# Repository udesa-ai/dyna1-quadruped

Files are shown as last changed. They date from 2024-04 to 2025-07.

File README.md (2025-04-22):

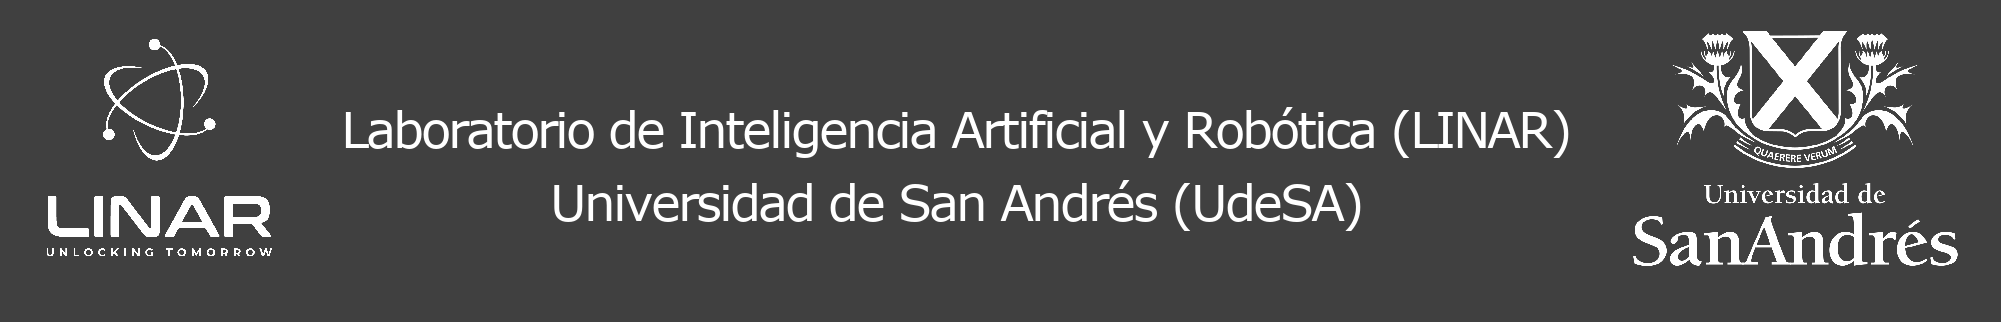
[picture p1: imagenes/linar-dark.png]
Linar

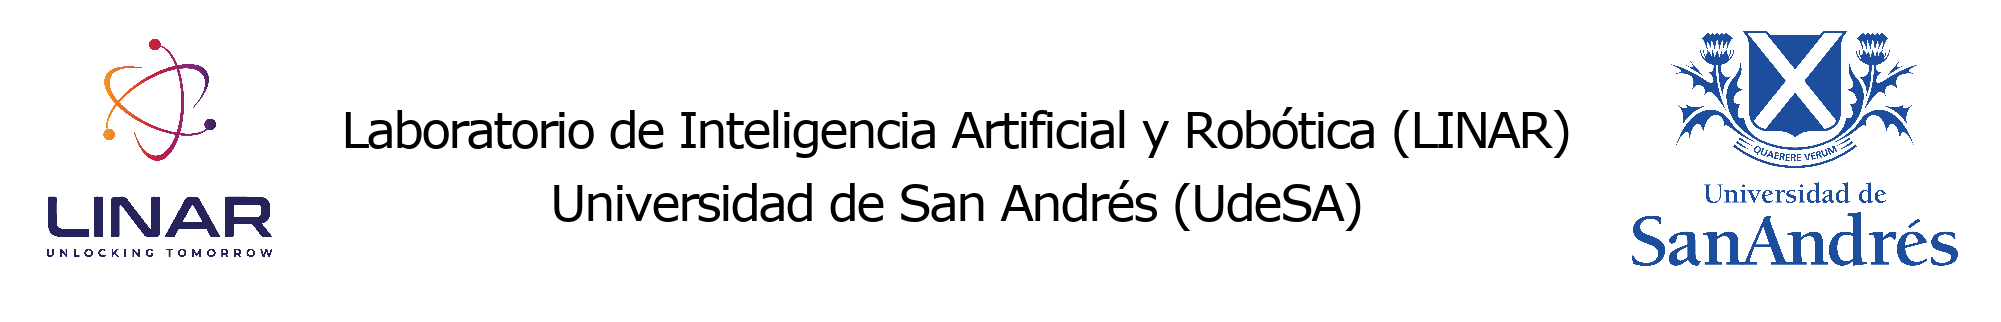
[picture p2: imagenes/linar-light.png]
Linar


<h1 align="center">Dyna1</h3>

<h3 align="center">Plataforma cuadrúpeda para evaluación de algorítmos de locomoción autónom</h3>

<p align="center">
  <a href="https://github.com#gh-light-mode-only">
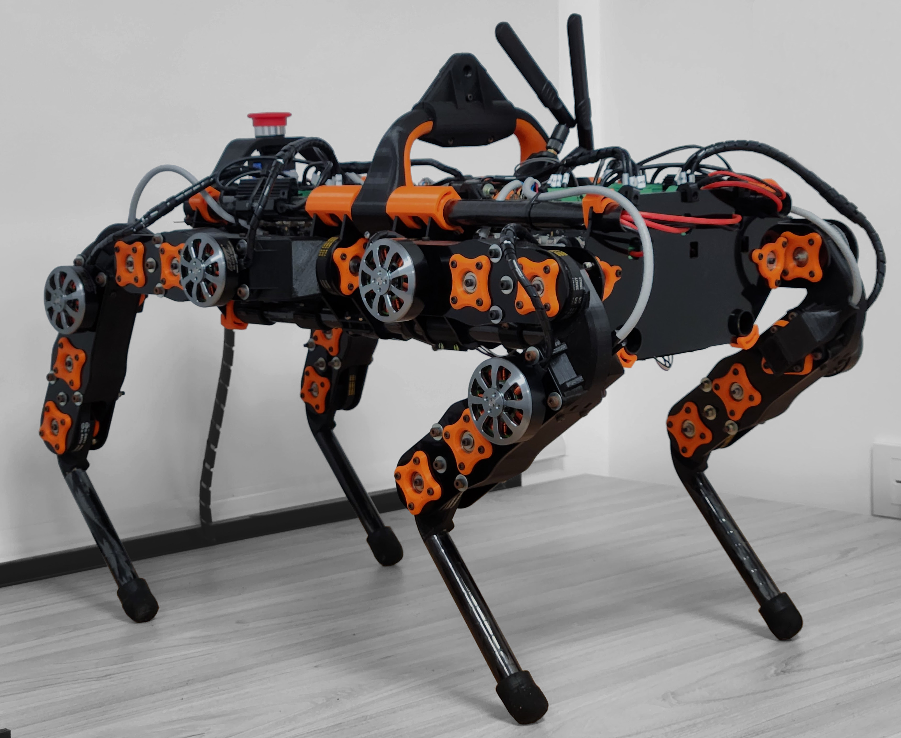
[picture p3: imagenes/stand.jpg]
    
  </a>
  <a href="https://github.com#gh-dark-mode-only">
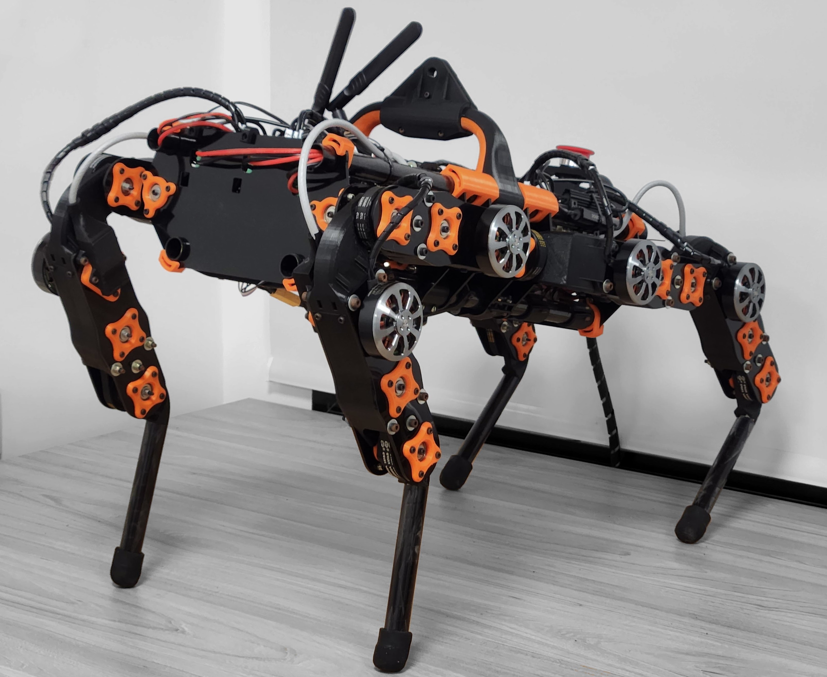
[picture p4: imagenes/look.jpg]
    
  </a>
</p>

## Descripción
<p align="justify"> Presentamos un nuevo diseño de cuadrúpedo de 12 grados de libertad, centrado en reducir el costo y la complejidad de fabricación, y maximizar el uso de componentes disponibles regionalmente. Para facilitar el ensamblado las piernas son modulares, y los motores están lo mas cerca posible del cuerpo para reducir su inercia. Se utilizan motores brushless junto a los controladores Odrive que permiten un control simple con su interfaz por CAN. El cuerpo contiene los motores de los hombros y toda la electónica necesaria para su funcionamiento. La estructura del mismo consta de cuatro barras y placas de acrílico transversales. Para controlar el cuadrúpedo se implementa el sistema operativo ROS2. Todos los proceso cruciales para el funcionamiento del robot se corren en la computadora a bordo, y los demas en la computadora externa. Se demostró experimentalmente que la pierna es capaz de saltar hasta 30 cm con un peso similar a un cuarto del cuerpo. La el período de control (12 ms) y medición (10 ms) se alcanza con un desvío estándar de 0.135 ms y 0.246 ms respectivamente, y las corriente RMS al caminar ronda los 15 A en el motor más exigido, por lo que no debería tener problemas de calentamiento. Se creó un simulador en Pybullet para evaluar algoritmos de autonomía de manera eficiente.  </p>

## Hardware

Los modelos 3d del robot pueden encontrarse en el siguiente link de drive: [LINK](https://drive.google.com/drive/folders/1FCLbqZc1CY9Qmqhhmpl-5FUQIIOlaMu-?usp=sharing).

En la carpeta se pueden encontrar los modelos en formato:
- Fusion 360 (.f3d)
- Step (.stp)

También podrán encontrar el listado de componentes en la carpeta de Hardware de este repositorio, como a su vez el instructivo de construcción y armado del robót.

## Software

La carpeta de Software contiene todas las clases de Python necesarias para el proceso de calibración e iniciación del cuadrúpedo, los paquetes de ROS2, y las instrucciones de uso.

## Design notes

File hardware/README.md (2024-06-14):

### Intervención de motores

Los motores brushless ML5010 y la mayoría de los motores brushless tienen el eje muy corto. 

<p align="center">
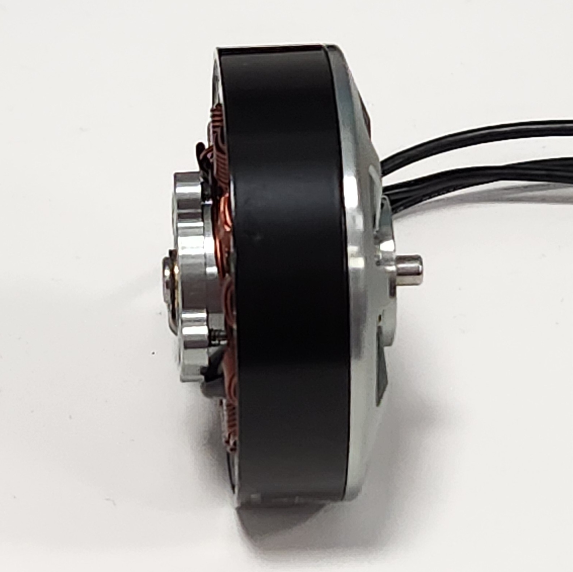
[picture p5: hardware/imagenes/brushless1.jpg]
  
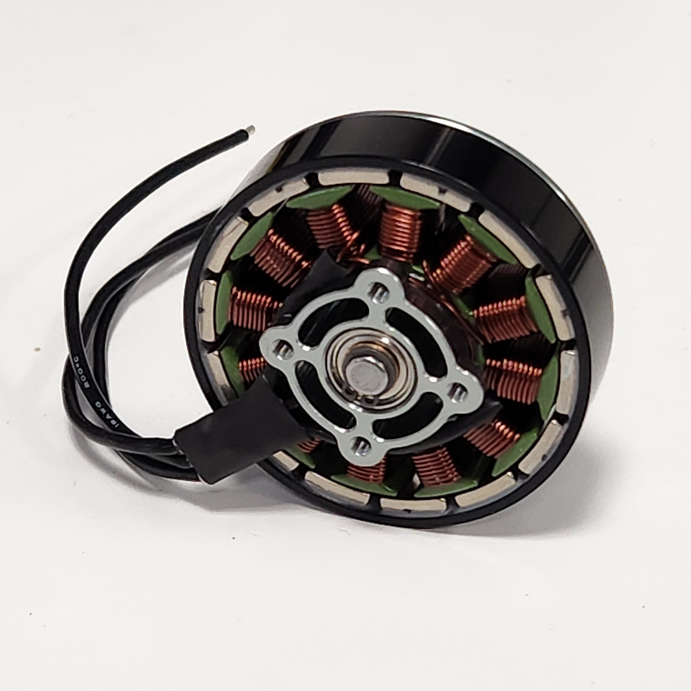
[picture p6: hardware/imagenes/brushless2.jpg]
  
</p>

Es por esto que es necesario removerlo y reemplazarlo por otro. En el caso de los ML5010 primero hay que remover la arandela que sostiene el cuerpo del motor. El eje se sostiene a la corona de imanes por medio de fricción y un prisionero. Un esquema del como debe ser el eje que lo reemplace puede encontrarse en esta carpeta. Se recomienda que le agregue conectores bullet a los cables de las tres faces para su posterior conección con los controladores.

### Metodología de armado general

Con el motoro intervenido podemos comenzar a armar el módulo reductor. A seguir se presenta la metodología estándar. Para formar todos los módulos o el cuerpo se podrá seguir estos pasos, modificando que piezas de utilizan. 

#### Paso 1

Primero se agregan las tuercas M3 a la pieza trasera del módulo, como a su vez los bulones que sostendrán al motor brushless. Se recomienda asegurar que los bulones pueden rotar libremente sin fuerza para facilitar la posterior instalación del motor.

<p align="center">
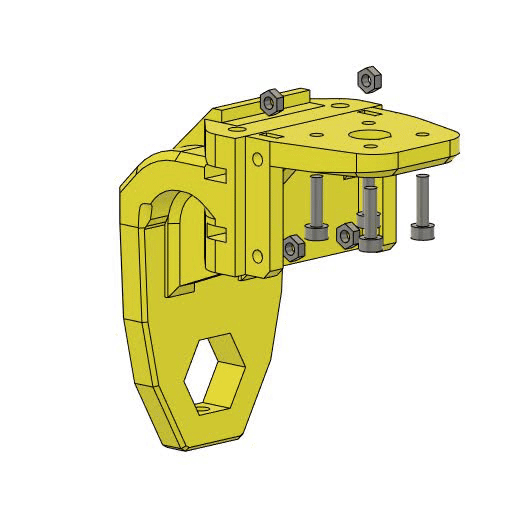
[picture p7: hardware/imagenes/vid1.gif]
  
</p>

#### Paso 2

A seguir se puede colocar la placa superior, los bulones que la sostienen y el motor brushless. Es importante colocar los bulones de la placa primero ya que con el motor instalado no se pueden agregar.

<p align="center">
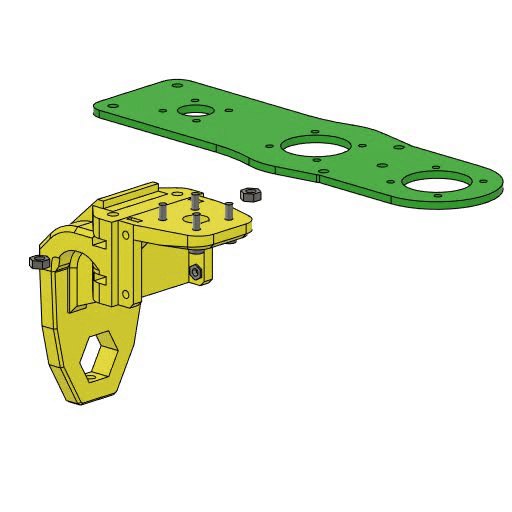
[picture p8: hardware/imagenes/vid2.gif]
  
</p>

#### Paso 3

Antes de colocar la primera polea se recomienda colocar las tuercas M2.5 y los bulones M2.5. Asegurese de que no se restrinja el paso del eje del motor dejando los bulones unos mm fuera de su rosca máxima.

<p align="center">
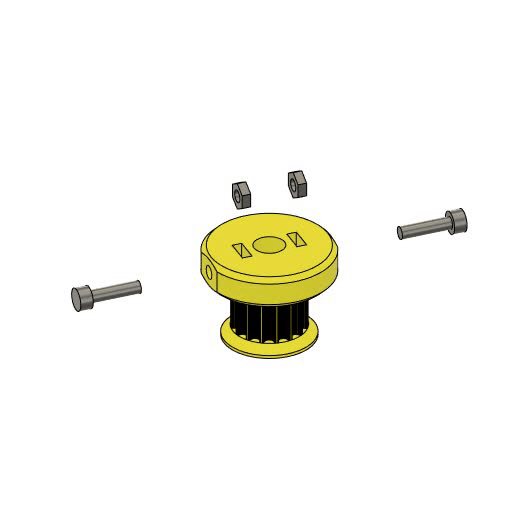
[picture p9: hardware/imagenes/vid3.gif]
  
</p>

#### Paso 4

Coloque las tuercas M2.5 en el alojamiento del encoder. Luego encastre el rodamiento 626zz. Inserte la polea inicial al eje del motor, agregue la correa y coloque la placa inferior. A seguir coloque el alojamiento y asegurelo con los bulones y tuercas M3.

<p align="center">
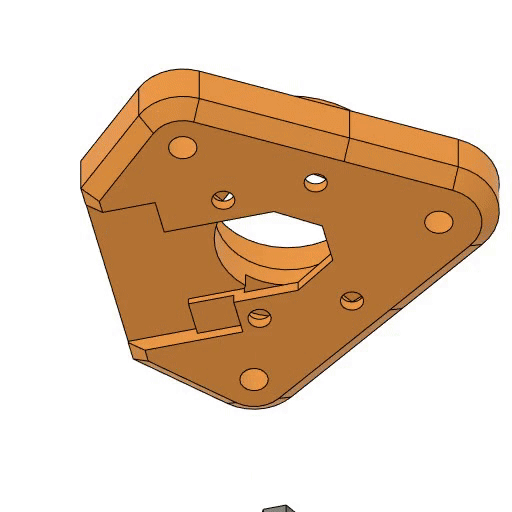
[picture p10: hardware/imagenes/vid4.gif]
  
</p>

#### Paso 5

Para facilitar la instalación del imán puede imprimir la pieza cilíndrica. Se recomienda además agregar una gota de loctite al momento de instalar para que el iman quede fijo al eje. Asegurese de que el pegamento no pase al rodamiento y que además el imán quede correctamente centrado para no perjudicar la medición del encoder.

<p align="center">
  
</p>

Ahora que ya colocó el imán se recomienda calibrar el Odrive y el motor corriendo las instrucciónes [oficiales](https://docs.odriverobotics.com/v/0.5.4/getting-started.html). No se olvide de configurar el index de CAN de los ejes del Odrive para poder comunicarse posteriormente por el bus CAN. El número de index de cada motor puede encontrarlo en el archivo "config.json".

#### Paso 6

Se recomienda colocar la polea central ya armada. Para eso agreuge los rodamientos a cada lado y comprima con el bulon M3. Luego inserte el rodamiento dentro del módulo. Asegurese de colocar correctamente la primera y segunda correa. Sostenga a la polea con los alojamientos. Para tensionar la correa puede rotar los alojamientos en las orientaciones marcadas. Cuanto mayor el número que apunta al motor más tensionada estará la correa. Para nuestro robot la primer polea se encuentra en posición 1 y la segunda en posición 2.

<p align="center">
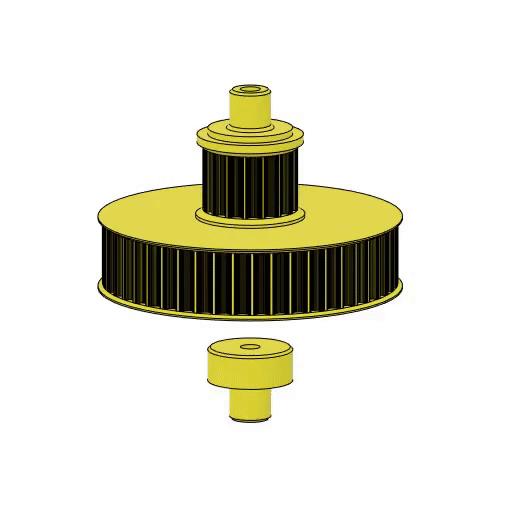
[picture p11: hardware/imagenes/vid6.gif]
  
</p>

#### Paso 7

Coloque la pieza central del módulo y la última polea. Asegurese de que quede bien encastrada la correa. Agregue los alojamientos y fíjelos. Agregue los bulones M4 y las placas laterales para rigidizar la estructura. No olvide atornillar los extremos traseros de las placas laterales.

<p align="center">
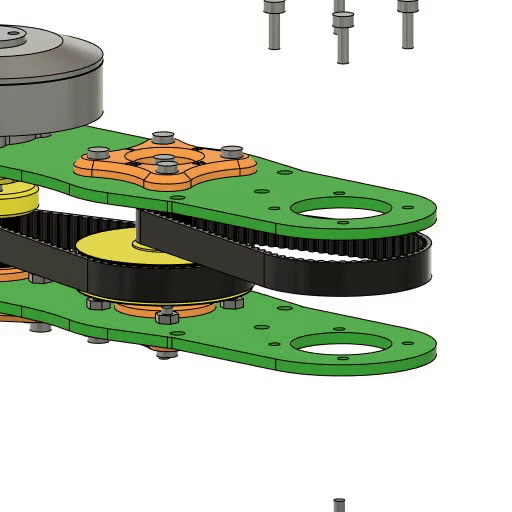
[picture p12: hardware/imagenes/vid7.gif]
  
</p>

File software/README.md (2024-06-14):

### Proceso de Iniciación

A seguir se presenta el paso a paso para inicializar el cuadrúpedo.

#### Paso 1

Corra el código de bash de "can_setup.sh" para activar el puerto CAN de la TX2:

```
./can_setup.sh
```

#### Paso 2

Reinicie los odrive con los motores en las posiciones que utilizará de referencia para cada inicialización.

```
python3 reboot.py
```

#### Paso 3

Una vez reiniciadas y orientadas las piernas corra el código "firmware_workaround.py" para activar el sensado de ángulo. 

```
python3 firmware_workaround.py
```

#### Paso 4

Si nunca calibró las posiciones de los encoder con la de las piernas corra el código de python "calibrate.py". A medida que le pregunte si está listo para calibrar cada pierna, posiciones las en el punto de referencia que decida utilizar.

```
python3 calibrate.py
```

#### Paso 5

Ahora con el robot calibrado y puesto en punto puede abrir el docker de Ubuntu 22 del Dockerfile y ahi correr ROS2 con los launch files.

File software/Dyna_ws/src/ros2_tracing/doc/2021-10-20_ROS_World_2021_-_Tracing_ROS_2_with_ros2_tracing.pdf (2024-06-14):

# Tracing ROS 2 with ros2_tracing

# Christophe Bédard

## ROS World 2021 October 20, 2021

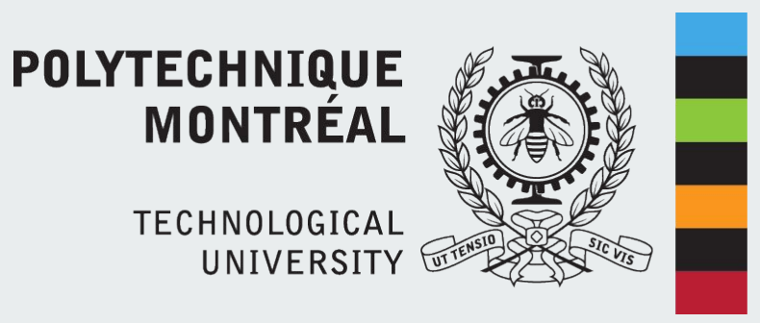
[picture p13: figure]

## DORSAL Laboratory Polytechnique Montréal

Tracing ROS 2 with ros2_tracing - Christophe Bédard

# Plan

### 1. Introduction 2. Context 3. Tracing & LTTng

4. ros2_tracing

### 5. Analysis 6. Demo 7. Conclusion 8. Questions

# Introduction

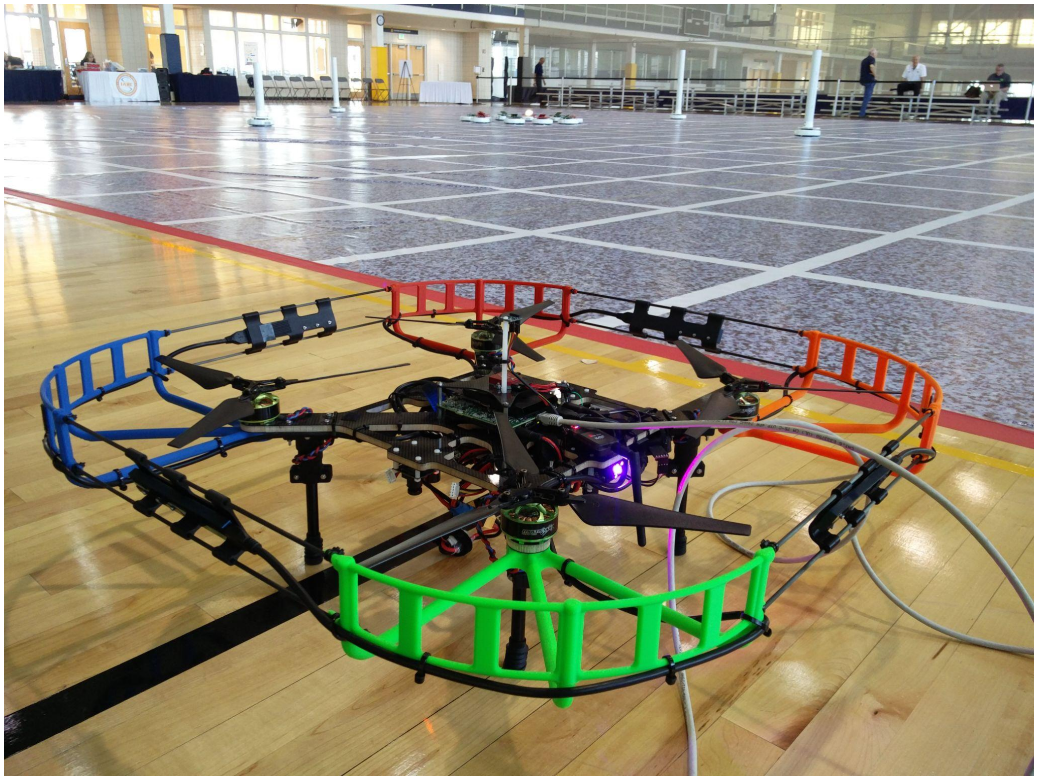
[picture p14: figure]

### - Robotics

- Many different types of applications
- Toys, commercial applications, industrial applications
- Safety-critical systems

### - ROS 2

- New capabilities
- Distributed systems
- Real-time constraints

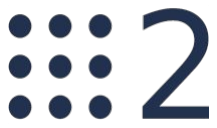
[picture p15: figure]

Context ● | Debugging and diagnostics tools ○ | Debugging: GDB ○ | Logs: ROS, printf() ○ | Introspection: rqt_graph ○ | Others: diagnostic_aggregator, libstatistics_collector ● | Distributed systems ○ | How to analyze a distributed system? ● | Real-time, production ● | Observability problems ○ | Observer effect ○ | Have to avoid influencing or affecting the application ● | Observing an application’s (lack of) determinism ○ | See Ingo Lütkebohle's ROSCon 2017 talk about determinism in ROS:

doi.org/10.36288/ROSCon2017-900789
- See also his talk at the ROSCon 2019 real-time workshop: apex.ai/roscon2019

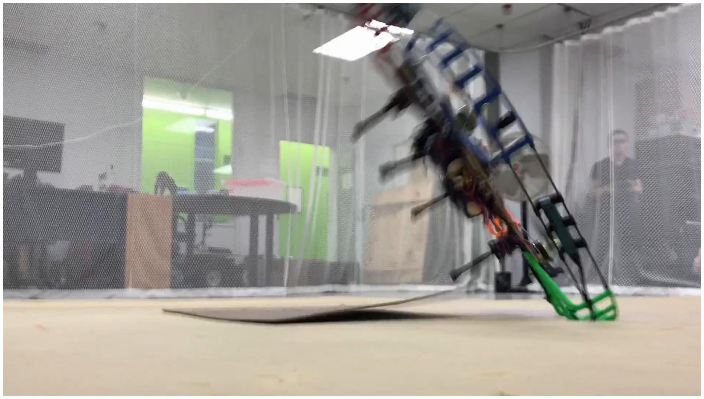
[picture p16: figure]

# Tracing

### - Goal: gather runtime execution information

- Low-level information
- OS and application

### - Useful when issues are hard to reproduce - Many different tracers with different features

- LTTng, perf, Ftrace, eBPF, DTrace, SystemTap, Event Tracing for Windows, etc.

### - Workflow (static instrumentation)

- Instrument an application with trace points
- Configure tracer, run the application
- Trace points generate events (information)
- Events make up a trace

### - We want to minimize the overhead!

- To use in production
- Observer effect

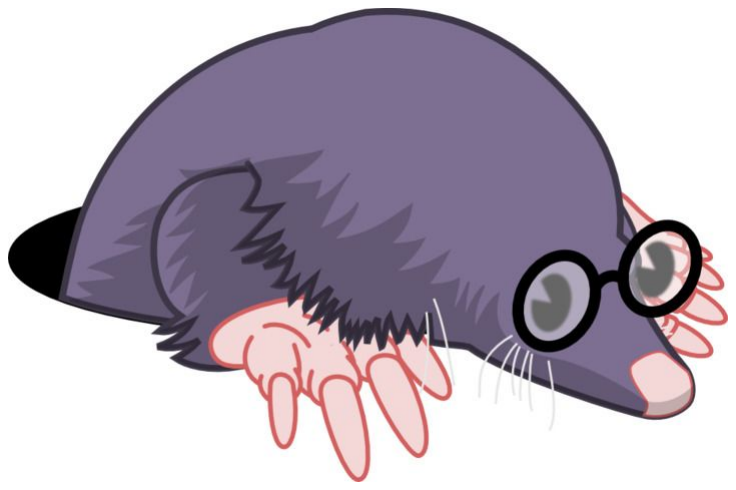
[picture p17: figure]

# LTTng

### - lttng.org - High-performance tracer

- Low overhead
- Userspace tracer + kernel tracer

### - Linux only - Instrumentation

- Built into the Linux kernel (e.g., sched_switch, net_dev_queue)
- Added statically to your application
- Or by LD_PRELOADing libraries

### - Trace data processing

- Online (live)
- Offline (more common & simpler)

# LTTng - example

$ lttng create ros2-session

$ lttng enable-event --kernel sched_switch

$ lttng enable-event --userspace ros2:rclcpp_publish

$ lttng enable-event --userspace ros2:*

$ lttng start

$ ros2 run package executable

$ lttng stop && lttng destroy

- Creating a tracing session, enabling trace events, tracing our application, and stopping

# LTTng - example (2)

$ babeltrace ros2-session/

sched_switch: { cpu_id = 1 }, { prev_comm = "swapper/1", prev_tid = 0, prev_prio = 20, prev_state = (

"TASK_RUNNING" : container = 0 ), next_comm = "test_ping", next_tid = 416160, next_prio = 20 }

ros2:callback_start: { cpu_id = 1 }, { callback = 0x541190, is_intra_process = 0 }

ros2:rclcpp_publish: { cpu_id = 1 }, { message = 0x5464F0 }

ros2:rcl_publish: { cpu_id = 1 }, { publisher_handle = 0x541A40, message = 0x5464F0 }

ros2:rmw_publish: { cpu_id = 1 }, { message = 0x5464F0 }

ros2:callback_end: { cpu_id = 1 }, { callback = 0x541190 }

### - Viewing the trace: each trace event has a name, timestamp, payload

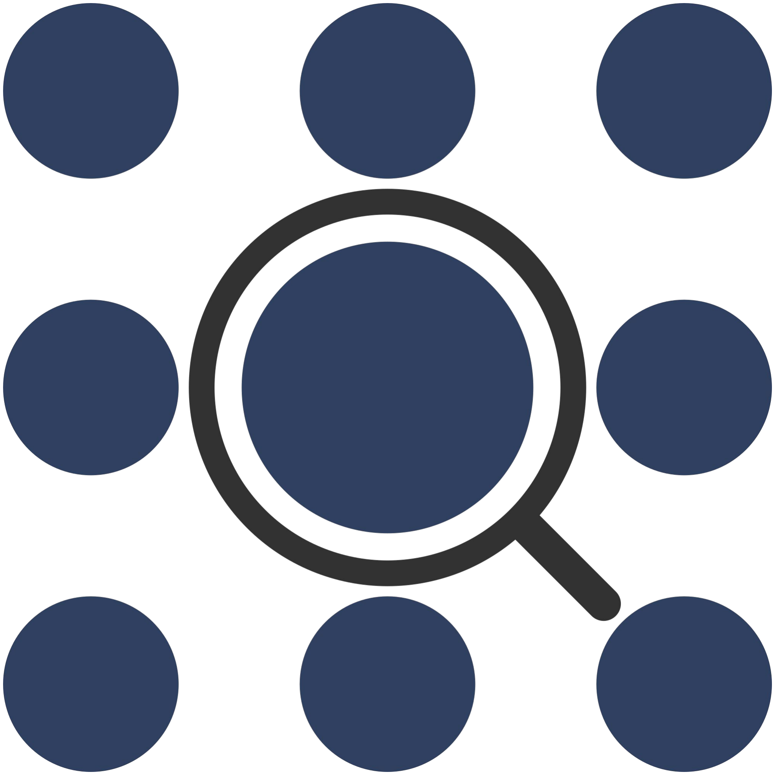
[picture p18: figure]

# ros2_tracing

### - gitlab.com/ros-tracing/ros2_tracing - Collection of tools - Closely integrated into ROS 2

- To promote use and adoption
- Since ROS 2 Eloquent (2019)
- Many improvements and additions since then

### - Tools to instrument the core of ROS 2 with LTTng

- rclcpp, rcl, rmw (rmw_cyclonedds* )

### - Tools to configure tracing with LTTng

- Command: ros2 trace
- Action for ROS 2 launch: Trace

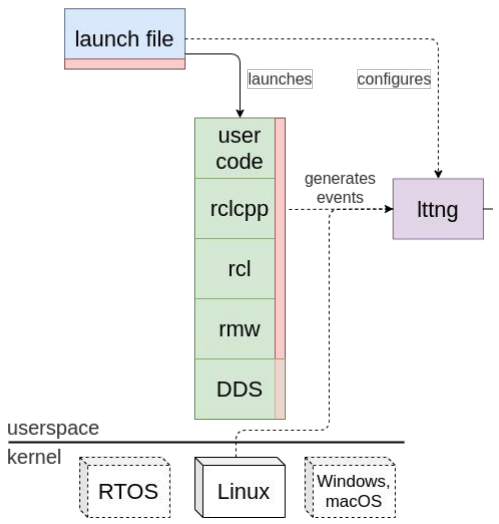
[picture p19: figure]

Figure 1. Instrumentation and general workflow.

# Tools - ros2 trace command

$ ros2 trace \

--session-name ros2-session \

--kernel sched_switch \

--ust ros2:rclcpp_publish ros2:*

writing tracing session to: /home/chris/.ros/tracing/ros2-session

press enter to start...

press enter to stop...

stopping & destroying tracing session

### - To easily start tracing - Starting & stopping is done manually

# Tools - Trace action for ROS 2 launch

from | launch | import | LaunchDescription
from | launch_ros.actions | import | Node
from | tracetools_launch.action | import | Trace
def | generate_launch_description():
return | LaunchDescription([

Trace(

session_name='ros2-session',

events_kernel=['sched_switch'],

events_ust=['ros2:rclcpp_publish', 'ros2:*'],

),

Node(

package='pkg',

executable='exe',

),

])

### - Starts tracing when launched - Stops tracing when exiting - Great for complex systems with multiple nodes

# Tools - Trace action for ROS 2 launch (2)

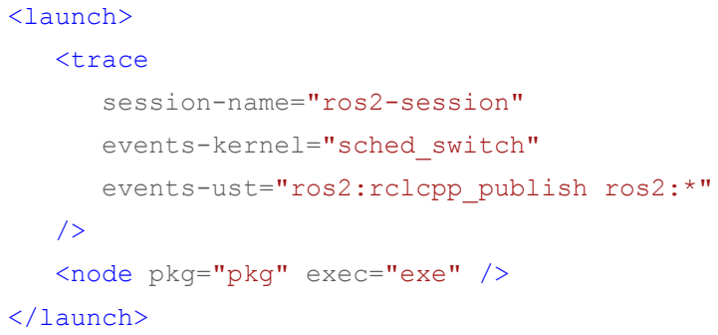
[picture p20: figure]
<launch>; <trace; session-name="ros2-session"; events-kernel="sched_switch"; events-ust="ros2:rclcpp_publish ros2:*"; <node; pkg="pkg"; exec="exe"; </launch>

launch:

- trace:
session-name: | ros2-session
events-kernel: | sched_switch
events-ust: | ros2:rclcpp_publish ros2:*
- node:
pkg: | pkg
exec: | exe

### - Also available in XML and YAML launch files

# Instrumentation

### - Only on Linux, not included in the binaries

- At least for now
- Install LTTng and (re)build the tracetools package

### - Instrumentation was designed to support multiple tracers

- Other tracers and/or OSes, eventually
- rclcpp, rcl, rmw, etc. → tracetools → LTTng

### - Design principles

- Want information about each layer & the interaction between them
- However, layers make it hard to get the full picture
- Need to gather small bits of information here and there
- Put it all together offline or externally

### - Real-time

- Applications generally have a non-real-time initialization phase
- We take advantage of this to collect as much information up front
- It lowers overhead in the real-time “steady state” phase

# Instrumentation (2)

- | Object instances ○ | Node, publisher, subscription, timer ● | Events ○ | Callback execution (subscription, timer) ○ | Message publication ○ | Message taking (for subscription callbacks) ○ | Lifecycle node state change ○ | Internal executor phases ○ | Etc. ● | Applies to most layers ○ | rclcpp, rcl, rmw ○ | DDS (work in progress with Eclipse Cyclone DDS)

ros2:rcl_node_init: { node_handle = | 0x🚀, rmw_handle = 0x..., node_name = "test_ping" }
ros2:rcl_publisher_init: { publisher_handle = | 0x, node_handle = 0x🚀, topic_name = "/ping", queue_depth = 10}
ros2:rcl_timer_init: { timer_handle = | 0x⏲, period = 500000000 }
ros2:rclcpp_timer_callback_added: { timer_handle = | 0x⏲, callback = 0x🤖 }
ros2:rclcpp_callback_register: { callback = | 0x🤖, symbol = "std::_Bind<void (PingNode::*(PingNode*))()>" }
ros2:rclcpp_timer_link_node: { timer_handle = | 0x⏲, node_handle = 0x🚀 }
ros2:callback_start: { callback = | 0x🤖, is_intra_process = 0 }
ros2:rclcpp_publish: { message = | 0x }
ros2:rcl_publish: { message = | 0x, publisher_handle = 0x }
ros2:rmw_publish: { message = | 0x }
ros2:callback_end: { callback = | 0x🤖 }

### - Ping node: a timer is used to publish a message periodically

# Instrumentation - example

# Overhead benchmark

- | Goal: measure tracing overhead in a ROS 2 context ○ | Mainly interested in a latency overhead ○ | Tool: gitlab.com/ApexAI/performance_test ● | Parameters ○ | Inter-process: 1 pub → 1 sub ○ | Publishing: 100 - 2000 Hz ○ | Messages: 1 - 256 KB ○ | Quality of service: reliable ○ | Eclipse Cyclone DDS ● | Setup ○ | Ubuntu Server 20.04.2 with PREEMPT_RT (5.4.3-rt1) ○ | Intel i7-3770 @ 3.40 GHz, 8 GB RAM ○ | SMT/Hyper-threading disabled (4 cores, 1 thread/core) ○ | SCHED_FIFO, RT priority 99, and other tuning ○ | Run for 20 minutes, discard the first 5 seconds

# Overhead benchmark - results

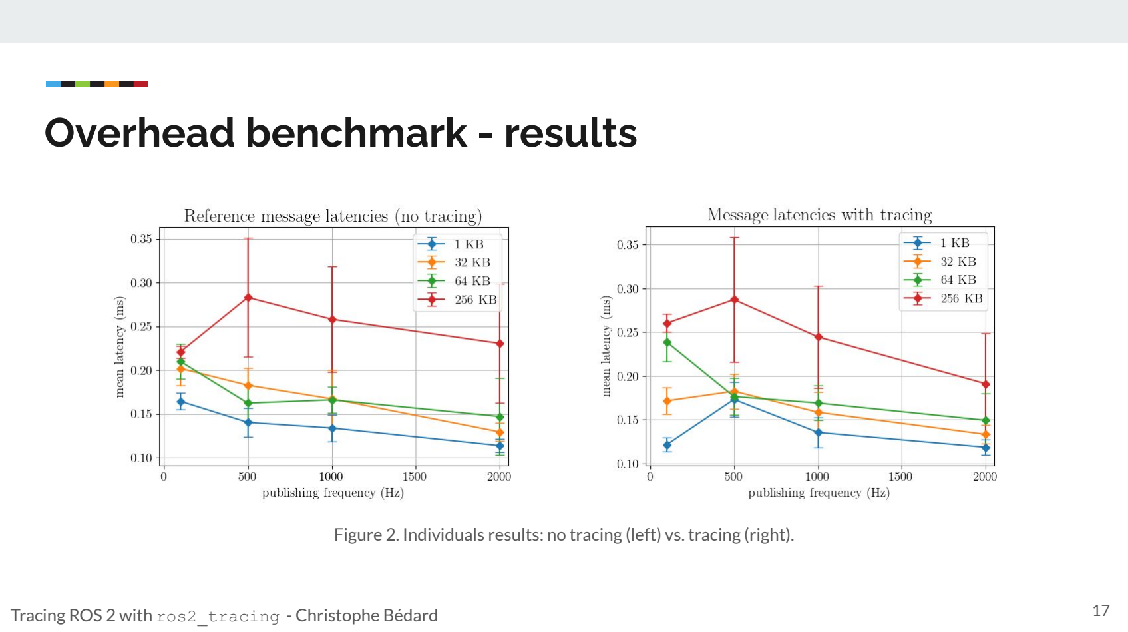
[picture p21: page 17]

Figure 2. Individuals results: no tracing (left) vs. tracing (right).

# Overhead benchmark - results (2)

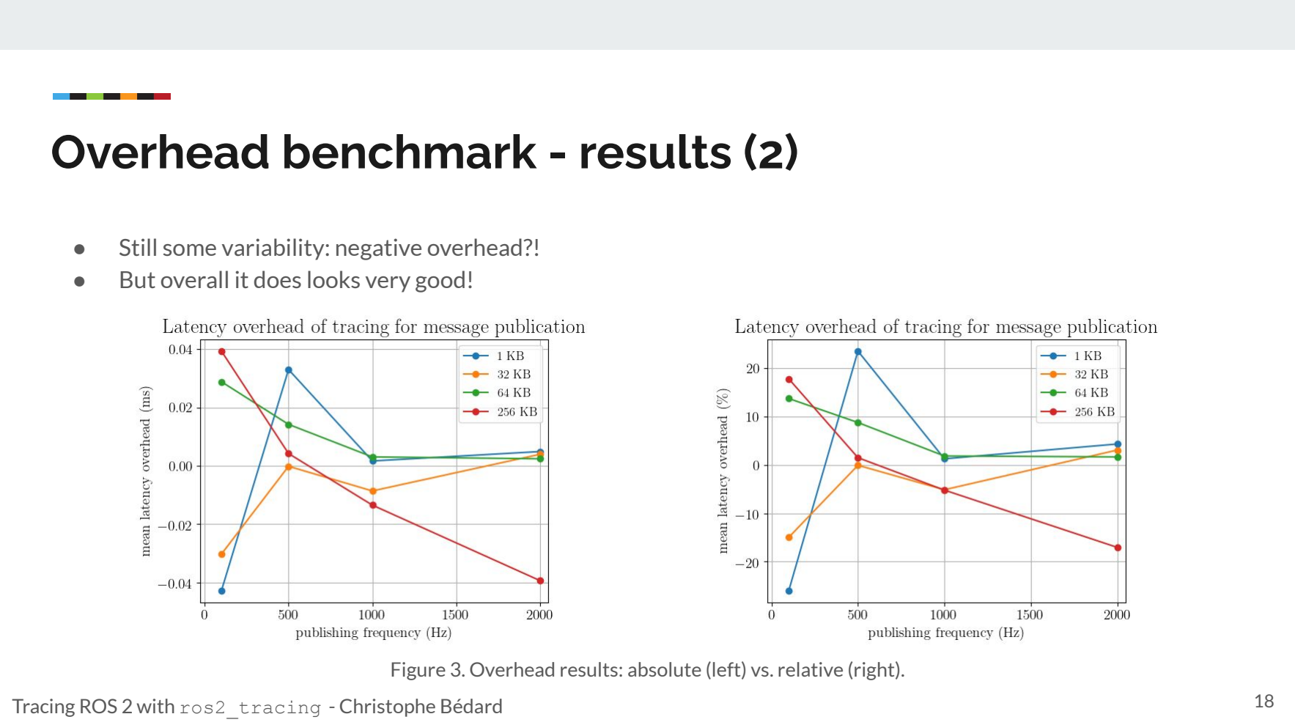
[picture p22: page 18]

### - Still some variability: negative overhead?! - But overall it does looks very good!

Figure 3. Overhead results: absolute (left) vs. relative (right).

# Analysis

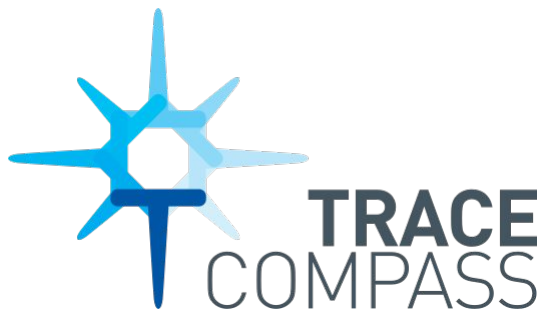
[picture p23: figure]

### - Many tools to analyze traces generated by LTTng

- babeltrace: babeltrace.org
- Trace Compass: tracecompass.org
- tracetools_analysis
- gitlab.com/ros-tracing/tracetools_analysis
- Goal: quick trace analysis
- Simple Python tool
- Pre-processes raw trace data, provides multiple 2D tables as pandas DataFrames
- Offers simple functions to analyze those DataFrames
- Use inside a Jupyter Notebook, or in a simple Python file

### - Advanced analyses

- Correlate ROS 2 trace events with events from the Linux kernel or other applications
- Analyze the aggregation of traces from multiple systems

# Analysis - example

import | tracetools_analysis; | import | bokeh
events = load_file('~/.ros/tracing/pingpong') | # Read the trace
handler = Ros2Handler.process(events) | # (Pre-)process the data

data_util = Ros2DataModelUtil(handler.data)

callback_symbols = data_util.get_callback_symbols() | # Extract callback functions

duration = bokeh.plotting.figure(...)

for | callback, symbol | in | callback_symbols.items(): | # For each callback...

owner_info = data_util.get_callback_owner_info(callback)

if | not | owner_info | or | '/parameter_events' | in | owner_info: | # | Filter out internal subscriptions

continue

duration_df = data_util.get_callback_durations(callback) | # | Get duration data for this callback
duration.line(x='timestamp', y='duration', legend=str(symbol), | # | Add to plot

source=bokeh.models.ColumnDataSource(duration_df))

bokeh.io.show(duration) | # Display final plot

### - Plot callback durations

# Analysis - example (2)

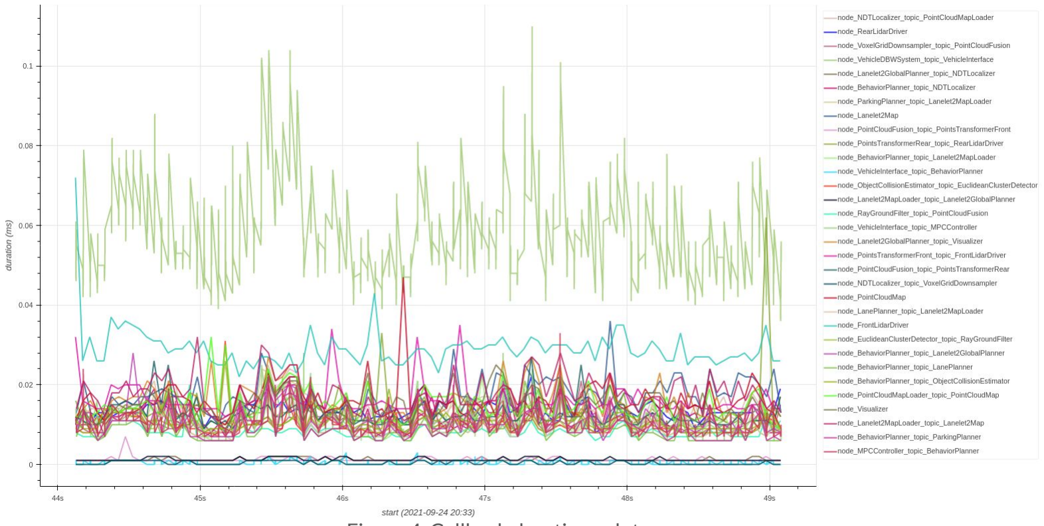
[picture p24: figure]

Figure 4. Callback durations plot.

# Analysis - example (3)

### - Using Trace Compass - Critical path analysis of a wget request - Computes dependencies between threads - Only using data from the Linux kernel

- Blocking system calls

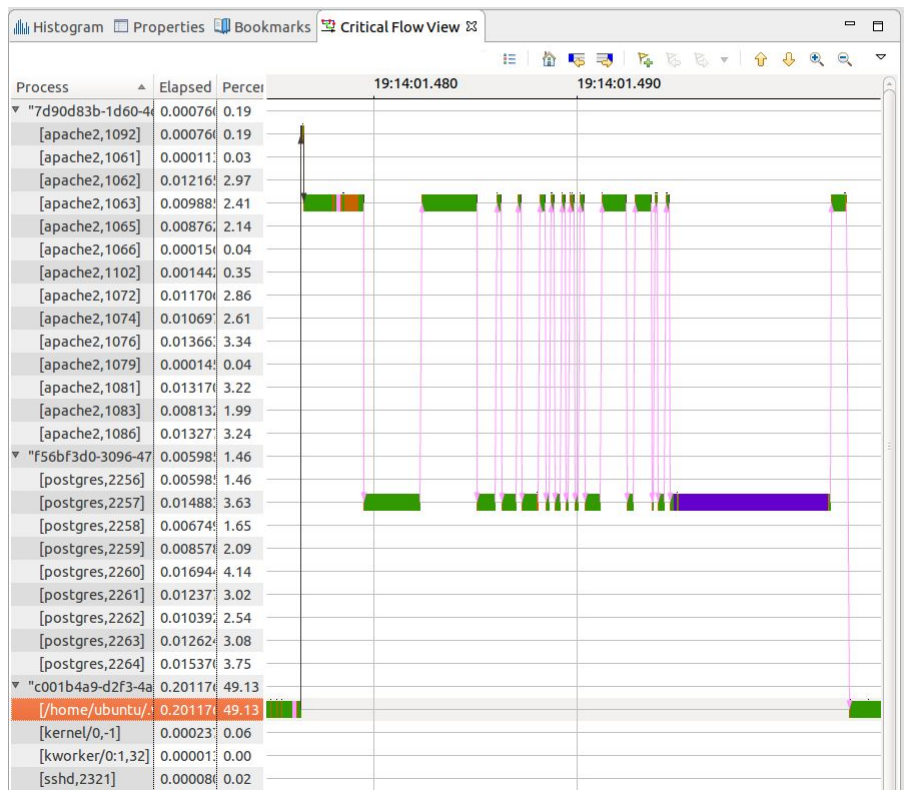
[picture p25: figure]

Figure 5. Critical path analysis using Trace Compass.

# Demo

### - Ping & pong nodes

- Nodes exchange N messages every M milliseconds T times, then exit

### - Link to instructions and Python code in a Jupyter Notebook

- github.com/christophebedard/ros-world-2021-demo

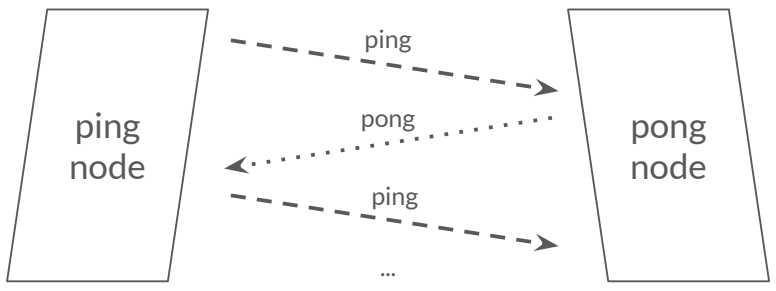
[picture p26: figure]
ping node; pong node; ping; pong

# Demo - results

### - Simple demo, ROS 2-level information only

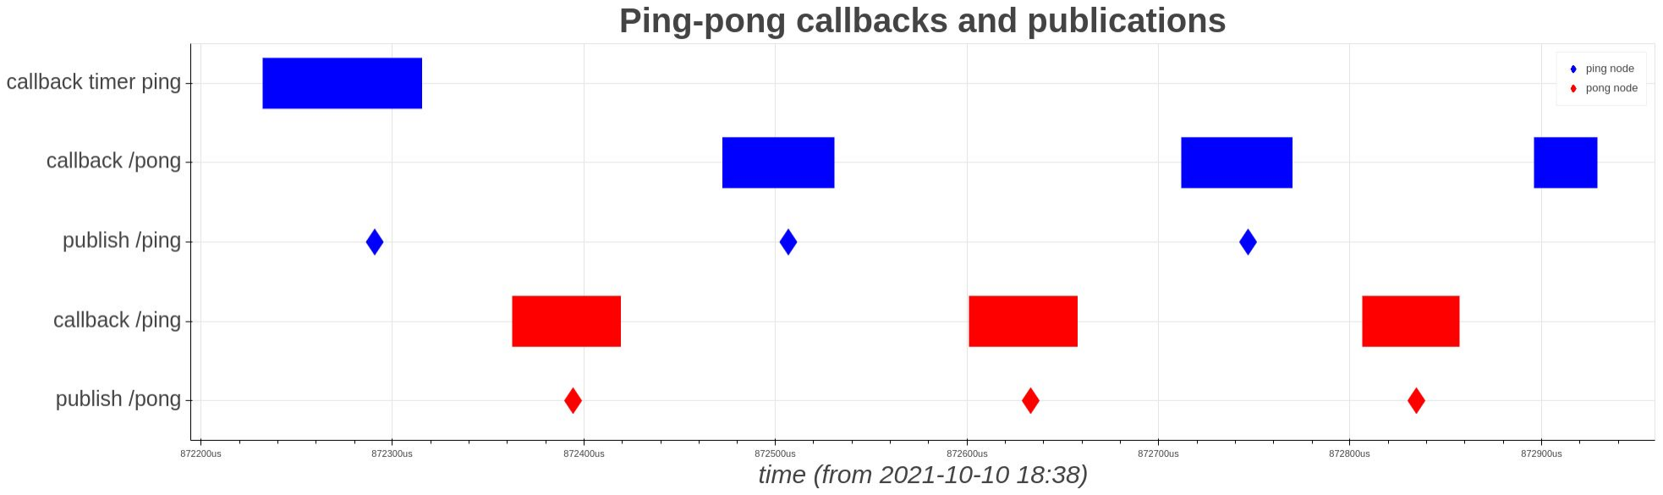
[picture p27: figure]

Figure 6. Results for 1 sequence.

# Demo - results (2)

- Still a lot of information & many possibilities, especially if we add DDS/middleware instrumentation!

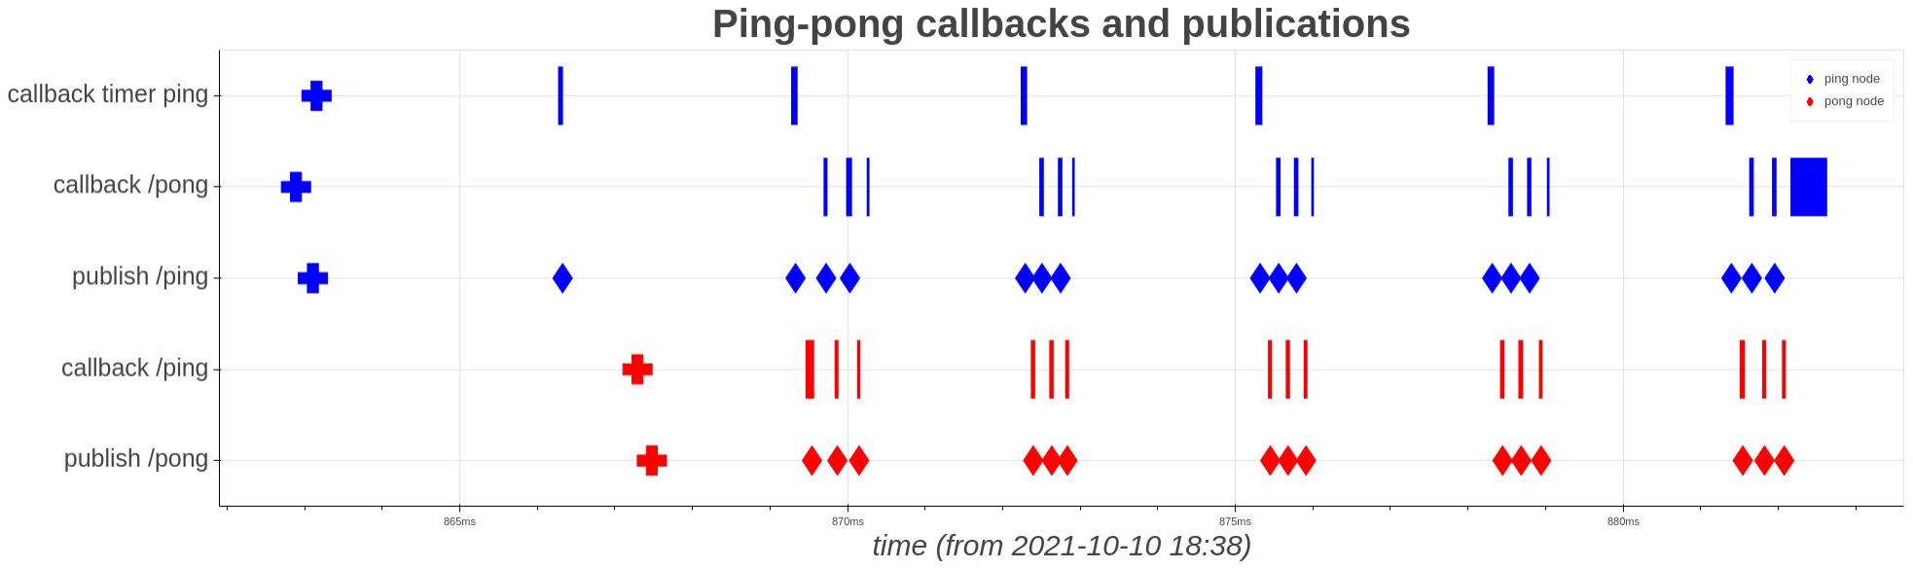
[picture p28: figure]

Figure 7. Overall demo results.

# Conclusion

### - Tracing

- Gather low-level runtime execution information
- Use a low overhead tracer
- ros2_tracing
- Instrumentation for the core of ROS 2
- Tools to trace with LTTng

### - Analysis

- Correlate OS events with ROS 2 events
- Analyze the aggregation of traces from multiple systems

### - Future

- Including the LTTng tracepoints in the Linux binaries
- Instrumentation
■ | Internal handling of messages, tracking messages across nodes
■ | DDS
- What would you like to see?!

Questions?; ● github.com/christophebedard; ● Important links; ○ gitlab.com/ros-tracing/ros2_tracing; ○ lttng.org ○ ros2_tracing tutorial in RTWG docs: bit.ly/RTWG_tracing_tutorial

- gitlab.com/ros-tracing/tracetools_analysis

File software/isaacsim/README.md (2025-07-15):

## Configuración del entorno para Dyna1 en Isaac Sim

### Isaac Lab
**Isaac Lab** es una librería construida sobre Isaac Sim que facilita el desarrollo de entornos de simulación para 
aprendizaje por refuerzo (RL), control óptimo y robótica en general. Se basa en gymnasium, y ofrece herramientas ya integradas para:

- Definir entornos personalizados tipo Gym.
- Entrenar políticas con algoritmos populares como PPO.
- Simular robots con interfaces limpias y separadas.
- Integrarse con librerías de RL como RL-Games, Stable-Baselines3, etc.

#### ¿Por qué usarlo?
- Estandariza cómo definís los entornos, sensores, recompensas y acciones.
- Aísla tu entorno personalizado del resto de Isaac Sim → más fácil de mantener y migrar.
- Ya tiene soporte para entrenamiento distribuido y acelerado por GPU.
- Facilita la transferencia del modelo a un robot real (sim2real).

### Isaac Extension Template
Es una plantilla modular creada para estructurar proyectos en Isaac Sim de forma escalable y mantenible:

Incluye:
- Separación clara entre código, assets, configuraciones.
- Soporte para definir extensiones de OmniIsaacGymEnvs, robots, tareas, sensores, etc.
- Integración con Isaac Lab out-of-the-box.

#### ¿Por qué usarlo?
- Permite trabajar en equipo con una arquitectura limpia y modular.
- Podés agregar o quitar componentes sin romper todo el proyecto.
- Si necesitás escalar, migrar o versionar tu entorno, esto evita el caos.

1. Clonar los repositorios necesarios
    
	    cd ~
	    https://github.com/isaac-sim/IsaacLabExtensionTemplate.git
	    https://github.com/isaac-sim/IsaacLab.git

2. Mover el entorno del Dyna1

    	mv dyna1-quadruped/software/isaacsim/DynabotIsaacTemplate IsaacLabExtensionTemplate/source

**DynabotIsaacTemplate** contiene toda la configuración específica del robot Dyna1 aislada de Isaac Lab. Esto significa que cualquier cambio en Isaac Lab no debería afectar nuestro entorno (en principio), manteniendo todo modular y desacoplado.

3. Editar el archivo en **IsaacLab/docker/docker-compose.yaml** y agregar estas líneas dentro de la sección binds del servicio (al final de esa lista):

		- type: bind
		source: /home/$USER/IsaacLabExtensionTemplate
		target: /workspace/IsaacLabExtensionTemplate

¿Qué hace esto?

- **type: bind:** Monta un volumen directamente desde el sistema de archivos del host.
- **source:** Ruta local donde está el proyecto (reemplazá $USER por tu nombre de usuario si no funciona).
- **target:** Ruta dentro del contenedor donde se verá esa carpeta.

4.  Iniciar el contenedor
   
   		./container.sh start

Es posible que la primera vez te aparezca este mensaje (ver Troubleshooting):

    X11 Forwarding is configured as '0' in '.container.cfg'.
	To enable X11 forwarding, set 'X11_FORWARDING_ENABLED=1' in '.container.cfg'.

5. Ingresar al contenedor

		./container.sh enter base

y una vez dentro del docker hacer:

    cd /workspace/IsaacLabExtensionTemplate/

6. Instalar todas las dependencias del Dyna1:

		python -m pip install -e source/DynabotIsaacTemplate

Si falla el paso anterior es poque probablemente antes haya que actualizar pip a la ultima version:

    /workspace/isaaclab/_isaac_sim/kit/python/bin/python3 -m pip install --upgrade pip

7. Si se quire correr la simulación en una máquina y visualizarla desde otra, exportá esta variable:

    	export LIVESTREAM=2

Esto es por si se esta usando una PC para correr el entrenamiento y se quiere visualizar el output de la simulacion desde otra.

8. Modificar import en script de entrenamiento

Editar la línea 68 del archivo IsaacLabExtensionTemplate/scripts/rsl_rl/train.py:

Antes:

	import ext_template.tasks  # noqa: F401

Después:
    
    import DynabotIsaacTemplate.tasks  # noqa: F401

9. Correr la simulación del Dyna1

Si todo fue bien (aunque probablemente algo haya que ajustar), lanzar la simulación con:

    python scripts/rsl_rl/train.py --task=Dyna1-Flat-v0 --headless --num_envs=32

Este comando indica que se va a lanzar la simulacion con terrenos **flat**, de manera **headless** con 32 robots. 

## Troubleshooting

- Si la simulación no se lanza en headless desde docker, puede ser que esté intentando hacer forward del GUI y crashee (porque tenés deshabilitado x11).
- Configurar esto en **isaacLab/docker/.container.cfg**:
  
      [X11]
      x11_forwarding_enabled = 0

- En uno de sus commits los genios de IsaacLab modificaron como hydra parsea atributos y tiro este error:

		usage: train.py [--help] [--hydra-help] [--version] [--cfg {job,hydra,all}] [--resolve] [--package PACKAGE] [--run] [--multirun] [--shell-completion] [--config-path CONFIG_PATH] [--config-name CONFIG_NAME] [--config-dir CONFIG_DIR] [--experimental-rerun EXPERIMENTAL_RERUN] [--info [{all,config,defaults,defaults-tree,plugins,searchpath}]] [overrides ...]
		train.py: error: unrecognized arguments: --/app/livestream/allowResize=false

- Por lo que debuggee esta linea en **train.py**:

		app_launcher = AppLauncher(args_cli)
 
 inyecta el argumento --/app/livestream/allowResize=false dentro de sys.argv. 
 
 - Agregar este filtrado después de la línea en la que se crea AppLauncher resuelve el problema.

		...
		app_launcher = AppLauncher(args_cli)
		simulation_app = app_launcher.app
		
		# Filter out AppLauncher-injected args before Hydra sees them
		sys.argv = [sys.argv[0]] + [arg for arg in hydra_args if not arg.startswith("--/")]
		...

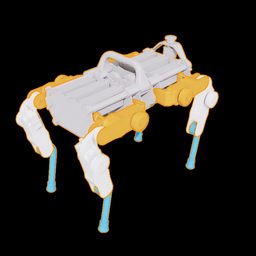
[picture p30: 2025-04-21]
software/isaacsim/DynabotIsaacTemplate/assets/urdf/dyna1/.thumbs/256x256/dyna1.usd.png

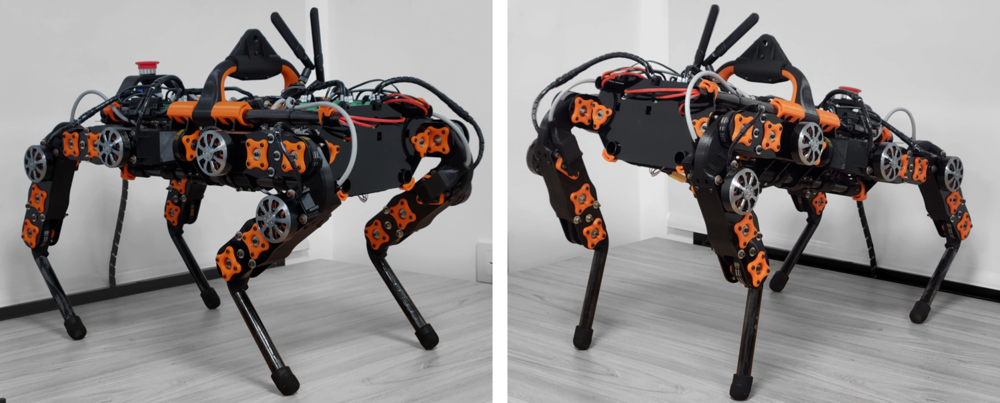
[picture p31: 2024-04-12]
imagenes/dog.png

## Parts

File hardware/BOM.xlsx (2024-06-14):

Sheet: Totales
Sub-Conjunto | Cantidad | Peso | Precio | Peso Total
Link 1 | 4 | 0.519 | $81.41 | 2.075 | Precio Dólar | 996.61
Link 2 | 4 | 0.515 | $80.92 | 2.058 | (al momento de armar la tabla)
Link 3 | 4 | 0.067 | $0.59 | 0.267
Cuerpo | 1 | 3.655 | $2672.97 | 3.655
 |  |  | $2835.89 | 8.055

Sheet: Modulo Link 1
Número | Nombre | Productor | Código Productor | Comentario | Link | Precio US$ | Precio AR$ | Peso [kg] | Cantidad | Total Precio US$ | Total Peso [kg]
1 | Motor | GARTT | ML 5010 300KV | - |  | $34.22 |  | 0.193 | 1 | $34.22 | 0.193
2 | Eje motor | UdeSA | - | 6mm de diámetro |  |  | $498.84 | 0.003 | 1 | $0.50 | 0.003
3 | Placa Superior |  | - | 3mm de espesor |  |  | $757.94 | 0.023 | 1 | $0.76 | 0.023
4 | Placa Inferior |  | - | 3mm de espesor |  |  | $719.14 | 0.022 | 1 | $0.72 | 0.022
5 | Correa | Gates | 3MR-255 | A definir en base a disponibilidad. Peso estimado |  |  | $11247.60 | 0.006 | 2 | $22.57 | 0.012
6 | Eje Central | I3D | - | Se asume densidad del 50% para PLA |  |  | $240.15 | 0.012 | 1 | $0.24 | 0.012
7 | Encoder | AMS | AS5047P | - | Link (https://www.mouser.co.uk/ProductDetail/ams/AS5047P-TS_EK_AB/?qs=Rt6VE0PE%2FOfJKFTMKo%252BL0Q==) | $15.75 |  | 0.017 | 1 | $15.75 | 0.017
8 | Alojamiento Rodamiento 1 | I3D | - | Se asume densidad del 50% para PLA |  |  | $62.31 | 0.003 | 4 | $0.25 | 0.013
9 | Rodamiento | SKF | W 626-2Z | - |  |  | $755.60 | 0.008 | 5 | $3.79 | 0.040
10 | Arandela M3 |  | - | - |  |  |  | 0.0004 | 8 | $0.00 | 0.004
11 | Tuerca M3 |  | 604 000 | - |  |  |  | 0.0004 | 22 | $0.00 | 0.009
12 | Tornillo Allen Boton M3x10 |  | OBAA00310 FOS | - |  |  |  | 0.0008 | 21 | $0.00 | 0.017
13 | Alojamiento Rodamiento 2 | I3D | - | Se asume densidad del 50% para PLA |  |  | $112.86 | 0.006 | 1 | $0.11 | 0.006
14 | Tuerca M2.5 |  | - | - |  |  |  | 0.0003 | 6 | $0.00 | 0.002
15 | Tornillo Allen Boton M2.5x5 |  | - | Revisar |  |  |  | 0.0005 | 4 | $0.00 | 0.002
16 | Engranaje Inicial | I3D | - | Se asume densidad del 50% para PLA |  |  | $53.32 | 0.003 | 1 | $0.05 | 0.003
17 | Tornillo Allen M2.5x12 |  |  | - |  |  |  | 0.0007 | 2 | $0.00 | 0.001
18 | Tapas plásticas | I3D | - | Se asume densidad del 50% para PLA |  |  | $572.83 | 0.0289 | 1 | $0.57 | 0.029
19 | Tornillo Allen Boton M3x16 |  | - | - |  |  |  | 0.0011 | 3 | $0.00 | 0.003
20 | Tornillo Allen Boton M4x16 |  | - | - |  |  |  | 0.002 | 5 | $0.00 | 0.011
21 | Toma Trasera | I3D | - | Se asume densidad del 50% para PLA |  |  | $877.26 | 0.044 | 1 | $0.88 | 0.044
22 | Tornillo Allen Boton M3x12 |  | - | - |  |  |  | 0.001 | 4 | $0.00 | 0.004
23 | Tuerca M4 |  | - | - |  |  |  | 0.001 | 4 | $0.00 | 0.003
24 | Barra de Aluminio 1 |  | - | - |  |  | $268.00 | 0.004 | 2 | $0.54 | 0.007
25 | Barra de Aluminio 2 |  | - | - |  |  | $172.00 | 0.002 | 1 | $0.17 | 0.002
26 | Tornillo Allen Boton M4x50 |  | - | - |  |  |  | 0.003 | 3 | $0.00 | 0.010
27 | Eje Hombro |  |  |  |  |  | $47.54 | 0.002 | 1 | $0.05 | 0.002
28 | Prisionero M3x6 |  | - | - |  |  |  | 0.0003 | 1 | $0.00 | 0.000301
29 | Tornillo Allen Boton M4x20 |  | - | - |  |  |  | 0.002 | 2 | $0.00 | 0.005
30 | Acomple Hombro | I3D | - | Se asume densidad del 50% para PLA |  |  | $224.35 | 0.011 | 1 | $0.23 | 0.011
31 | Arandela M4 |  |  |  |  |  |  | 0.001 | 3 | $0.00 | 0.002
32 | Tornillo Allen M3x50 |  |  |  |  |  |  | 0.003 | 2 | $0.00 | 0.007
 |  |  |  |  |  |  |  |  |  | $0.00 | 0.000
 |  |  |  |  |  |  |  |  |  | $0.00 | 0.000
 |  |  |  |  |  |  |  |  |  | $0.00 | 0.000
 |  |  |  |  |  |  |  |  |  | $0.00 | 0.000
 |  |  |  |  |  |  |  |  |  | $0.00 | 0.000
 |  |  |  |  |  |  |  |  |  | $0.00 | 0.000
 |  |  |  |  |  |  |  |  |  | $81.41 | 0.5187806093

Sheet: Modulo Link 2
Número | Nombre | Productor | Código Productor | Comentario | Link | Precio US$ | Precio AR$ | Peso [kg] | Cantidad | Total Precio US$ | Total Peso [kg]
1 | Motor | GARTT | ML 5010 300KV | - |  | $34.22 |  | 0.193 | 1 | $34.22 | 0.193
2 | Eje motor | UdeSA | - | 6mm de diámetro |  |  | $498.84 | 0.003 | 1 | $0.50 | 0.003
3 | Placa Superior | Mundo Acrilico | - | 3mm de espesor |  |  | $757.94 | 0.023 | 1 | $0.76 | 0.023
4 | Placa Inferior | Mundo Acrilico | - | 3mm de espesor |  |  | $719.14 | 0.022 | 1 | $0.72 | 0.022
5 | Correa | Gates | 3MR-255 | A definir en base a disponibilidad. Peso estimado |  |  | $11247.60 | 0.006 | 2 | $22.57 | 0.012
6 | Eje Central | I3D | - | Se asume densidad del 50% para PLA |  |  | $240.15 | 0.012 | 1 | $0.24 | 0.012
7 | Encoder | AMS | AS5047P | - | Link (https://www.mouser.co.uk/ProductDetail/ams/AS5047P-TS_EK_AB/?qs=Rt6VE0PE%2FOfJKFTMKo%252BL0Q==) | $15.75 |  | 0.017 | 1 | $15.75 | 0.017
8 | Alojamiento Rodamiento 1 | I3D | - | Se asume densidad del 50% para PLA |  |  | $62.31 | 0.003 | 4 | $0.25 | 0.013
9 | Rodamiento | SKF | W 626-2Z | - |  |  | $755.60 | 0.008 | 5 | $3.79 | 0.040
10 | Arandela M3 | Fercor | - | - |  |  |  | 0.0004 | 4 | $0.00 | 0.002
11 | Tuerca M3 | Tubolon S.A. | 604 000 | - |  |  |  | 0.0004 | 21 | $0.00 | 0.009
12 | Tornillo Allen Boton M3x10 | Fercor | OBAA00310 FOS | - |  |  |  | 0.0008 | 20 | $0.00 | 0.016
14 | Alojamiento Rodamiento 2 | I3D | - | Se asume densidad del 50% para PLA |  |  | $113.18 | 0.006 | 1 | $0.11 | 0.006
15 | Tuerca M2.5 | Fercor | - | - |  |  |  | 0.0003 | 6 | $0.00 | 0.002
16 | Tornillo Allen Boton M2.5x5 | Fercor | - | Revisar |  |  |  | 0.0005 | 4 | $0.00 | 0.002
17 | Engranaje Inicial | I3D | - | Se asume densidad del 50% para PLA |  |  | $53.32 | 0.003 | 1 | $0.05 | 0.003
18 | Tornillo Allen M2.5x12 |  |  | - |  |  |  | 0.0007 | 2 | $0.00 | 0.001
19 | Tapas plásticas | I3D | - | Se asume densidad del 50% para PLA |  |  | $572.83 | 0.0289 | 1 | $0.57 | 0.029
20 | Tornillo Allen Boton M3x16 |  | - | - |  |  |  | 0.0011 | 3 | $0.00 | 0.003
21 | Tornillo Allen Boton M4x20 | Fercor | - | - |  |  |  | 0.003 | 2 | $0.00 | 0.005
22 | Tornillo Allen Boton M4x16 | Fercor | - | - |  |  |  | 0.002 | 2 | $0.00 | 0.004
23 | Toma Trasera | I3D | - | Se asume densidad del 50% para PLA |  |  | $1234.45 | 0.062 | 1 | $1.24 | 0.062
24 | Tornillo Allen Boton M3x12 | Fercor | - | - |  |  |  | 0.001 | 4 | $0.00 | 0.004
25 | Tuerca M4 | Fercor | - | - |  |  |  | 0.001 | 7 | $0.00 | 0.006
26 | Cubre Encoder | I3D |  | Se asume densidad del 50% para PLA |  |  | $130.30 | 0.007 | 1 | $0.13 | 0.007
27 | Arandela M4 |  |  |  |  |  |  | 0.001 | 6 | $0.00 | 0.003
28 | Tornillo Allen M4x50 |  |  |  |  |  |  | 0.004 | 3 | $0.00 | 0.011
29 | Tornillo Allen M3x50 |  |  |  |  |  |  | 0.003 | 2 | $0.00 | 0.007
30 |  |  |  |  |  |  |  | 0.000 | 0 | $0.00 | 0.000
31 |  |  |  |  |  |  |  | 0.000 | 0 | $0.00 | 0.000
32 |  |  |  |  |  |  |  | 0.000 | 0 | $0.00 | 0.000
33 |  |  |  |  |  |  |  | 0.000 | 0 | $0.00 | 0.000
 |  |  |  |  |  |  |  |  |  | $80.92 | 0.5146186831

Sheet: Link 3
Número | Nombre | Productor | Código Productor | Comentario | Link | Precio US$ | Precio AR$ | Peso [kg] | Cantidad | Total Precio US$ | Total Peso [kg]
1 | Barra carbono |  | - | - |  |  |  | 0.017 | 1 | $0.00 | 0.017
2 | Pie |  | - | - |  |  |  | 0.020 | 1 | $0.00 | 0.020
3 | Rodilla | I3D | - | Se asume densidad del 50% para PLA |  |  | $592.57 | 0.030 | 1 | $0.59 | 0.030
4 |  |  |  |  |  |  |  |  |  | $0.00
5
 |  |  |  |  |  |  |  |  |  | $0.59 | 0.066728

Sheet: Cuerpo
Número | Nombre | Productor | Código Productor | Comentario | Link | Precio US$ | Precio AR$ | Peso [kg] | Cantidad | Total Precio US$ | Total Peso [kg]
1 | Barra |  | - | - |  |  |  | 0.069 | 4 | $0.00 | 0.278
2 | Placa v1 |  |  |  |  |  | $2033.46 | 0.068 | 2 | $4.08 | 0.135
3 | Placa v2 |  |  |  |  |  | $1961.88 | 0.065 | 4 | $7.87 | 0.261
4 | Motor | GARTT | ML 5010 300KV | - |  | $34.22 |  | 0.193 | 4 | $136.88 | 0.772
5 | Eje motor | UdeSA | - | 6mm de diámetro |  |  | $498.84 | 0.003 | 4 | $2.00 | 0.012
6 | Drivers | Odrive | ODRIVE V3.6 | - | Link (https://odriverobotics.com/shop/odrive-v36) | $259.00 |  | 0.085 | 6 | $1554.00 | 0.510
7 | Correa | Gates | 3MR-255 | A definir en base a disponibilidad. Peso estimado |  |  | $11247.60 | 0.006 | 8 | $90.29 | 0.048
8 | Engranaje Central | I3D | - | Se asume densidad del 50% para PLA |  |  | $240.15 | 0.012 | 4 | $0.96 | 0.049
9 | Encoder | AMS | AS5047P | - | Link (https://www.mouser.co.uk/ProductDetail/ams/AS5047P-TS_EK_AB/?qs=Rt6VE0PE%2FOfJKFTMKo%252BL0Q==) | $15.75 |  | 0.017 | 4 | $63.00 | 0.069
10 | Alojamiento Rodamiento 1 | I3D | - | Se asume densidad del 50% para PLA |  |  | $62.31 | 0.003 | 16 | $1.00 | 0.050
11 | Rodamiento | SKF | W 626-2Z | - |  |  | $755.60 | 0.008 | 24 | $18.20 | 0.192
12 | Alojamiento Rodamiento 2 | I3D | - | Se asume densidad del 50% para PLA |  |  | $113.18 | 0.006 | 4 | $0.45 | 0.023
13 | Barra de Aluminio 1 |  | - | - |  |  | $268.00 | 0.004 | 2 | $0.54 | 0.007
14 | Tuerca M3 |  | 604 000 | - |  |  |  | 0.0004 | 129 | $0.00 | 0.055
15 | Tornillo Allen Boton M3x10 |  | OBAA00310 FOS | - |  |  |  | 0.0008 | 68 | $0.00 | 0.054
16 | Tuerca M2.5 |  | - | - |  |  |  | 0.0003 | 24 | $0.00 | 0.007
17 | Tornillo Allen Boton M2.5x5 |  | - | Revisar |  |  |  | 0.0005 | 16 | $0.00 | 0.007
18 | Engranaje Inicial | I3D | - | Se asume densidad del 50% para PLA |  |  | $53.32 | 0.003 | 4 | $0.21 | 0.011
19 | Tornillo Allen Boton M3x12 |  | - | - |  |  |  | 0.001 | 37 | $0.00 | 0.034
20 | Acople Rodamiento 1 | I3D | - | Se asume densidad del 50% de PLA |  |  | $47.20 | 0.002 | 4 | $0.19 | 0.010
21 | Acople Rodamiento 2 | I3D | - | Se asume densidad del 50% de PLA |  |  | $40.61 | 0.002 | 4 | $0.16 | 0.008
22 | Tornillo Allen M2.5x12 |  |  | - |  |  |  | 0.0007 | 8 | $0.00 | 0.005
23 | Tornillo Allen Boton M3x16 |  | - | - |  |  |  | 0.0011 | 50 | $0.00 | 0.053
24 | Fijador 7 | I3D |  | Se asume densidad del 50% de PLA |  |  | $36.55 | 0.002 | 8 | $0.29 | 0.015
25 | Fijador Odrive | I3D |  | Se asume densidad del 50% de PLA |  |  | $17.46 | 0.001 | 12 | $0.21 | 0.011
26 | Fijador 1 | I3D |  | Se asume densidad del 50% de PLA |  |  | $143.45 | 0.007 | 4 | $0.58 | 0.029
27 | Handle 1 | I3D |  | Se asume densidad del 50% de PLA |  |  | $1059.76 | 0.054 | 1 | $1.06 | 0.054
28 | Handle 2 | I3D |  | Se asume densidad del 50% de PLA |  |  | $989.50 | 0.050 | 1 | $0.99 | 0.050
29 | Holder soga | I3D |  | Se asume densidad del 50% de PLA |  |  | $402.73 | 0.020 | 2 | $0.81 | 0.041
30 | Tornillo Allen M4x50 |  |  |  |  |  |  | 0.004 | 3 | $0.00 | 0.011
31 | Tornillo Allen M3x50 |  |  |  |  |  |  | 0.003 | 8 | $0.00 | 0.027
32 | Engranaje Final | I3D |  | Se asume densidad del 50% de PLA |  |  | $254.91 | 0.013 | 4 | $1.02 | 0.051
33 | Arandela M4 |  |  |  |  |  |  | 0.001 | 40 | $0.00 | 0.021
34 | Arandela M3 | Fercor | - | - |  |  |  | 0.0004 | 4 | $0.00 | 0.002
35 | Tuerca M4 |  | - | - |  |  |  | 0.001 | 20 | $0.00 | 0.016
36 | Tornillo Allen M4x50 |  |  |  |  |  |  | 0.004 | 12 | $0.00 | 0.042
37 | Antena Holder | I3D |  | Se asume densidad del 50% de PLA |  |  | $109.55 | 0.006 | 1 | $0.11 | 0.006
38 | Fijador 4 | I3D |  | Se asume densidad del 50% de PLA |  |  | $258.85 | 0.013 | 2 | $0.52 | 0.026
39 | Fijador 3 | I3D |  | Se asume densidad del 50% de PLA |  |  | $275.89 | 0.014 | 2 | $0.55 | 0.028
40 | Fijador 2 | I3D |  | Se asume densidad del 50% de PLA |  |  | $432.61 | 0.022 | 2 | $0.87 | 0.044
41 | Fijador 4 vg | I3D |  | Se asume densidad del 50% de PLA |  |  | $350.62 | 0.018 | 2 | $0.70 | 0.035
42 | Jetson TX2 + Quasar |  |  |  |  | $745.00 |  | 0.217 | 1 | $745.00 | 0.217
43 | Jetson cage 1 | I3D |  | Se asume densidad del 50% de PLA |  |  | $468.73 | 0.024 | 1 | $0.47 | 0.024
44 | Jetson cage 2 | I3D |  | Se asume densidad del 50% de PLA |  |  | $237.46 | 0.012 | 1 | $0.24 | 0.012
45 | Jetson holder 1 | I3D |  | Se asume densidad del 50% de PLA |  |  | $252.35 | 0.013 | 1 | $0.25 | 0.013
46 | Jetson holder 2 | I3D |  | Se asume densidad del 50% de PLA |  |  | $265.91 | 0.013 | 1 | $0.27 | 0.013
47 | Baterry Holder | I3D |  | Se asume densidad del 50% de PLA |  |  | $528.64 | 0.027 | 4 | $2.12 | 0.107
48 | Tornillo Allen M3x20 |  |  |  |  |  |  | 0.001 | 2 | $0.00 | 0.003
49 | IMU holder | I3D |  | Se asume densidad del 50% de PLA |  |  | $121.35 | 0.006 | 1 | $0.12 | 0.006
50 | IMU |  |  | - |  | $34.95 |  | 0.003 | 1 | $34.95 | 0.003
51 | Cable Holders | I3D |  | Se asume densidad del 50% de PLA |  |  | $388.89 | 0.020 | 2 | $0.78 | 0.039
52 | Sostenedor de Boton de emergencia | I3D |  | Se asume densidad del 50% de PLA |  |  | $419.78 | 0.021 | 1 | $0.42 | 0.021
53 | Boton de Emergencia | I3D |  | Se asume densidad del 50% de PLA |  |  | $778.38 | 0.039 | 1 | $0.78 | 0.039
54 |  |  |  |  |  |  |  |  |  | $0.00 | 0.000
55 |  |  |  |  |  |  |  |  |  | $0.00 | 0.000
56 |  |  |  |  |  |  |  |  |  | $0.00 | 0.000
 |  |  |  |  |  |  |  |  |  | $2672.97 | 3.654968954

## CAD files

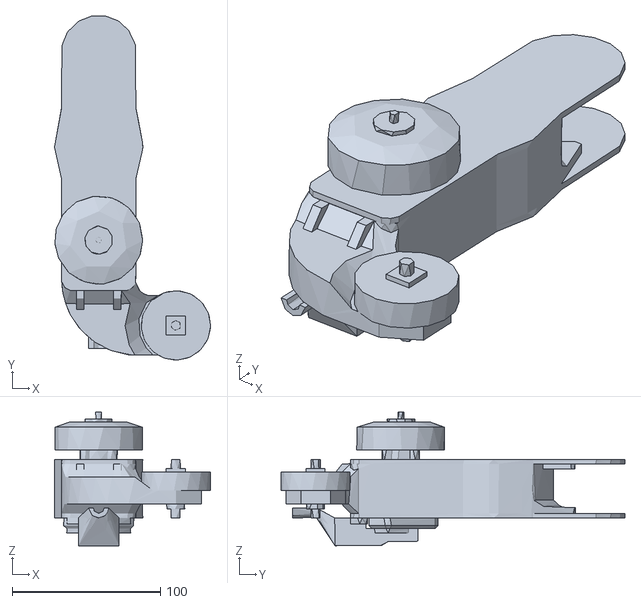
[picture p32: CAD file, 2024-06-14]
software/Dyna_ws/src/py_simulator/stl/arm2.stl
105.2 x 231.8 x 90.0

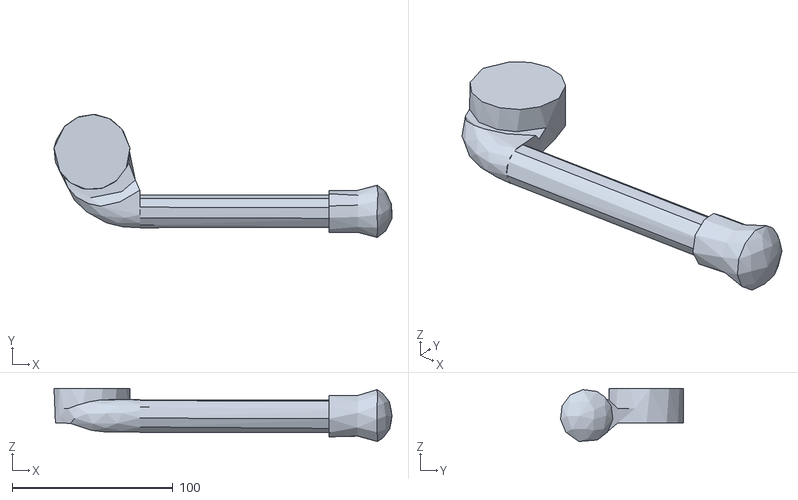
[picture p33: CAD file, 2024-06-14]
software/Dyna_ws/src/py_simulator/stl/foot2.stl
210.0 x 76.5 x 32.9

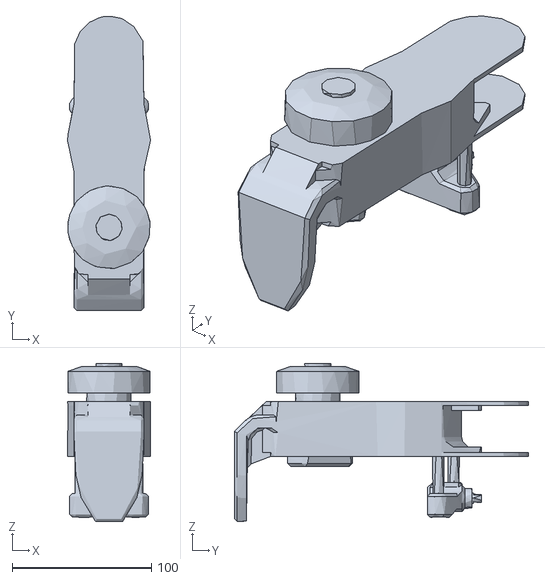
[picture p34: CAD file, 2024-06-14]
software/Dyna_ws/src/py_simulator/stl/shoulder.stl
59.7 x 211.0 x 113.4

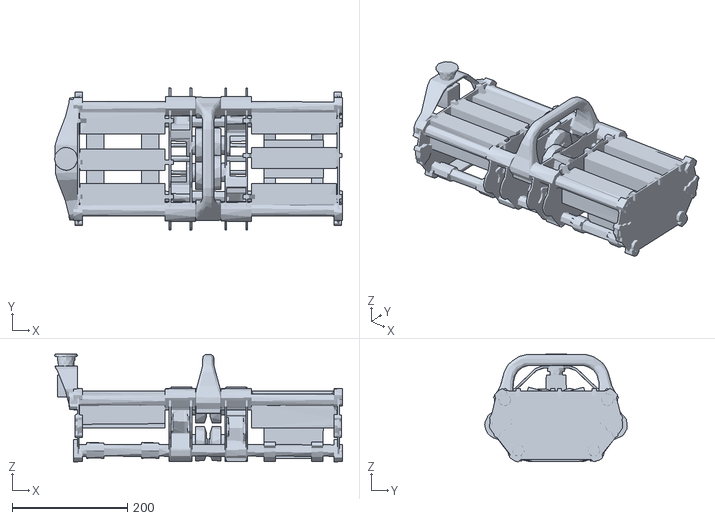
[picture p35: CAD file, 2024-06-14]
software/Dyna_ws/src/py_simulator/stl/Body.stl
499.1 x 247.1 x 187.1

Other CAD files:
software/Dyna_ws/src/py_simulator/stl/arm1.stl
software/Dyna_ws/src/py_simulator/stl/foot1.stl

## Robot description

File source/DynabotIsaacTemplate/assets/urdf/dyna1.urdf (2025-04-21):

<?xml version='1.0' encoding='utf-8'?>
<robot name="dyna1">
  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

  <link name="base_link">
    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
    <inertial>
      <mass value="3.671" />
			<origin rpy="0 0 0" xyz="0.00545 0.00008 0.008719" />
      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
    </inertial>
  </link>

  <link name="front_left_shoulder_link">
    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
    <inertial>
      <mass value="0.505084" />
			<origin rpy="0 0 0" xyz="-0.000225 -0.096893 0.058205" />
      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
    </inertial>
  </link>


  <link name="front_left_arm_link">
    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
    <inertial>
      <mass value="0.500063"/>
			<origin rpy="0 0 0" xyz="0.049769 0.079064 0.017355"/>
      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
    </inertial>
  </link>

  <link name="front_left_hand_link">
    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
    <inertial>
      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
      <mass value="0.066814"/>
			<origin rpy="0 0 0" xyz="0.07927 -0.025916 -0.001911"/>
      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
    </inertial>
  </link>

  <joint name="base_to_front_left_shoulder" type="revolute">
    <parent link="base_link"/>
    <child link="front_left_shoulder_link"/>
    <axis xyz="0 -1 0"/>
    <origin rpy="-1.57079632679 -1.57079632679 0" xyz="0.2352235 0.0985 0"/>
    <limit effort="100.0" lower="-0.6051" upper="0.6051" velocity="100"/>
    <dynamics damping="0.0" friction="0"/>
  </joint>

  <joint name="front_left_shoulder_to_arm" type="revolute">
    <parent link="front_left_shoulder_link"/>
    <child link="front_left_arm_link"/>
    <axis xyz="0 0 -1"/>
    <origin rpy="0 0 1.84649081579" xyz="0 0 0.0435"/>
    <limit effort="100.0" lower="-1.3135" upper="2.4337" velocity="100"/>
    <dynamics damping="0.0" friction="0"/>
  </joint>

  <joint name="front_left_arm_to_hand" type="revolute">
    <parent link="front_left_arm_link"/>
    <child link="front_left_hand_link"/>
    <axis xyz="0 0 1"/>
    <origin rpy="3.14159265359 0 1.103929191" xyz="0.0519 0.183458 0"/>
    <limit effort="100.0" lower="-0.8515" upper="2.6321" velocity="100"/>
    <dynamics damping="0.0" friction="0"/>
  </joint>

 




  <link name="front_right_shoulder_link">
    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
    <inertial>
      <mass value="0.505084"/>
			<origin rpy="0 0 0" xyz="-0.000225 -0.096893 0.058205"/>
      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
    </inertial>
  </link>

  <link name="front_right_arm_link">
    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
    <inertial>
      <mass value="0.500063"/>
			<origin rpy="0 0 0" xyz="-0.049769 0.079064 0.017355"/>
      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
    </inertial>
  </link>

  <link name="front_right_hand_link">
    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
    <inertial>
      <mass value="0.066814"/>
			<origin rpy="0 0 0" xyz="0.07927 -0.025916 0.001911"/>
      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
    </inertial>
  </link>

  <joint name="base_to_front_right_shoulder" type="revolute">
    <parent link="base_link"/>
    <child link="front_right_shoulder_link"/>
    <axis xyz="0 -1 0"/>
    <origin rpy="0 1.57079632679 -1.57079632679" xyz="0.2352235 -0.0985 0"/>
    <limit effort="100.0" lower="-0.6051" upper="0.6051" velocity="100"/>
    <dynamics damping="0.0" friction="0"/>
  </joint>

  <joint name="front_right_shoulder_to_arm" type="revolute">
    <parent link="front_right_shoulder_link"/>
    <child link="front_right_arm_link"/>
    <axis xyz="0 0 1"/>
    <origin rpy="0 0 -1.84649081579" xyz="0 0 0.0435"/>
    <limit effort="100.0" lower="-1.3135" upper="2.4337" velocity="100"/>
    <dynamics damping="0.0" friction="0"/>
  </joint>

  <joint name="front_right_arm_to_hand" type="revolute">
    <parent link="front_right_arm_link"/>
    <child link="front_right_hand_link"/>
    <axis xyz="0 0 1"/>
    <origin rpy="0 0 2.03766346259" xyz="-0.0519 0.183458 0"/>
    <limit effort="100.0" lower="-0.8515" upper="2.6321" velocity="100"/>
    <dynamics damping="0.0" friction="0"/>
  </joint>





  <link name="back_left_shoulder_link">
    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
    <inertial>
      <mass value="0.505084"/>
			<origin rpy="0 0 0" xyz="-0.000225 -0.096893 0.058205"/>
      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
    </inertial>
  </link>

  <link name="back_left_arm_link">
    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
    <inertial>
      <mass value="0.500063"/>
			<origin rpy="0 0 0" xyz="-0.049769 0.079064 0.017355"/>
      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
    </inertial>
  </link>

  <link name="back_left_hand_link">
    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
    <inertial>
      <mass value="0.066814"/>
			<origin rpy="0 0 0" xyz="0.07927 -0.025916 0.001911"/>
      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
    </inertial>
  </link>

  <joint name="base_to_back_left_shoulder" type="revolute">
    <parent link="base_link"/>
    <child link="back_left_shoulder_link"/>
    <axis xyz="0 1 0"/>
    <origin rpy="0 1.57079632679 1.57079632679" xyz="-0.2352235 0.0985 0"/>
    <limit effort="100.0" lower="-0.6051" upper="0.6051" velocity="100"/>
    <dynamics damping="0.0" friction="0"/>
  </joint>

  <joint name="back_left_shoulder_to_arm" type="revolute">
    <parent link="back_left_shoulder_link"/>
    <child link="back_left_arm_link"/>
    <axis xyz="0 0 -1"/>
    <origin rpy="0 0 -1.84649081579" xyz="0 0 0.0435"/>
    <limit effort="100.0" lower="-2.4337" upper="1.3135" velocity="100"/>
    <dynamics damping="0.0" friction="0"/>
  </joint>

  <joint name="back_left_arm_to_hand" type="revolute">
    <parent link="back_left_arm_link"/>
    <child link="back_left_hand_link"/>
    <axis xyz="0 0 1"/>
    <origin rpy="3.14159265359 0 1.655318169" xyz="-0.0519 0.183458 0"/>
    <limit effort="100.0" lower="-0.30696" upper="3.17664" velocity="100"/>
    <dynamics damping="0.0" friction="0"/>
  </joint>



  <link name="back_right_shoulder_link">
    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
    <inertial>
      <mass value="0.505084"/>
			<origin rpy="0 0 0" xyz="-0.000225 -0.096893 0.058205"/>
      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
    </inertial>
  </link>

  <link name="back_right_arm_link">
    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
    <inertial>
      <mass value="0.500063"/>
			<origin rpy="0 0 0" xyz="0.049769 0.079064 0.017355"/>
      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
    </inertial>
  </link>

  <link name="back_right_hand_link">
    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
    <inertial>
      <mass value="0.066814"/>
			<origin rpy="0 0 0" xyz="0.07927 -0.025916 0.001911"/>
      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
    </inertial>
  </link>

  <joint name="base_to_back_right_shoulder" type="revolute">
    <parent link="base_link"/>
    <child link="back_right_shoulder_link"/>
    <axis xyz="0 1 0"/>
    <origin rpy="0 -1.57079632679 1.57079632679" xyz="-0.2352235 -0.0985 0"/>
    <limit effort="100.0" lower="-0.6051" upper="0.6051" velocity="100"/>
    <dynamics damping="0.0" friction="0"/>
  </joint>

  <joint name="back_right_shoulder_to_arm" type="revolute">
    <parent link="back_right_shoulder_link"/>
    <child link="back_right_arm_link"/>
    <axis xyz="0 0 1"/>
    <origin rpy="0 0 1.84649081579" xyz="0 0 0.0435"/>
    <limit effort="100.0" lower="-2.4337" upper="1.3135" velocity="100"/>
    <dynamics damping="0.0" friction="0"/>
  </joint>

  <joint name="back_right_arm_to_hand" type="revolute">
    <parent link="back_right_arm_link"/>
    <child link="back_right_hand_link"/>
    <axis xyz="0 0 1"/>
    <origin rpy="0 0 1.48627448459" xyz="0.0519 0.183458 0"/>
    <limit effort="100.0" lower="-0.30696" upper="3.17664" velocity="100"/>
    <dynamics damping="0.0" friction="0"/>
  </joint>


</robot>

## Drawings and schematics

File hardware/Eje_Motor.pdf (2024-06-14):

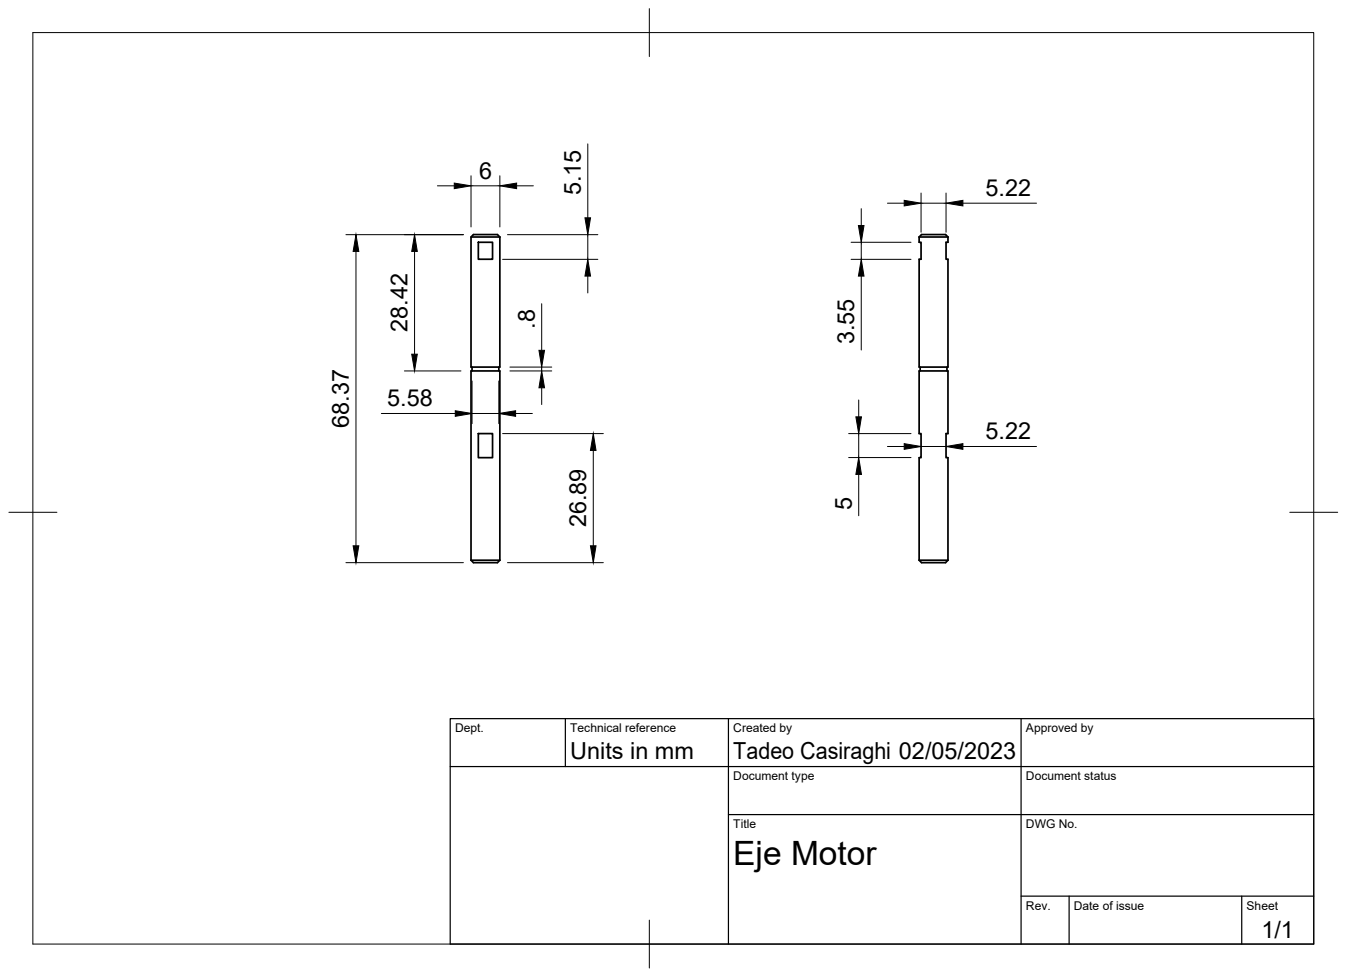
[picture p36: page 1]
Units in mm; Tadeo Casiraghi 68.37

Dept. | Technical reference | Created by 02/05/2023 | Approved by

Document type | Document status

Title Eje Motor | DWG No.

Rev. | Date of issue | Sheet 1/1

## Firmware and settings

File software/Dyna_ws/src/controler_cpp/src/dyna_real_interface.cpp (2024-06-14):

#include "dyna_real_interface.hpp"

using std::placeholders::_1;

RealInterface::RealInterface(): Node("dyna_real_interface")
{
    RCLCPP_INFO(rclcpp::get_logger("rclcpp"),"Staring Interface Node");
    /* ############## Parameters ############## */
    this->declare_parameter("MAX_CURRENT",10);
    MAX_CURRENT = (uint8_t) this->get_parameter("MAX_CURRENT").as_int();
    
    /* Controller Params */
    this->declare_parameter("STEPLENGTH_SCALE", 0.0f);
    STEPLENGTH_SCALE = (float) this->get_parameter("STEPLENGTH_SCALE").as_double();

    this->declare_parameter("Z_SCALE_CTRL",0.0f);
    Z_SCALE_CTRL = (float) this->get_parameter("Z_SCALE_CTRL").as_double();

    this->declare_parameter("RPY_SCALE",0.0f);
    RPY_SCALE = (float) this->get_parameter("RPY_SCALE").as_double();
    
    this->declare_parameter("SV_SCALE",0.0f);
    SV_SCALE = (float) this->get_parameter("SV_SCALE").as_double();
    
    this->declare_parameter("CHPD_SCALE",0.0f);
    CHPD_SCALE = (float) this->get_parameter("CHPD_SCALE").as_double();
    
    this->declare_parameter("YAW_SCALE",0.0f);
    YAW_SCALE = (float) this->get_parameter("YAW_SCALE").as_double();

    /* FIXED */
    this->declare_parameter("BaseStepVelocity",0.0f);
    BaseStepVelocity = (float) this->get_parameter("BaseStepVelocity").as_double();
    StepVelocity = BaseStepVelocity;

    /* Stock, use Bumpers to change */
    this->declare_parameter("Tswing",0.0f);
    BaseSwingPeriod = (float) this->get_parameter("Tswing").as_double();
    SwingPeriod = BaseSwingPeriod;

    this->declare_parameter("SwingPeriod_LIMITS", std::vector<float>({0.0f, 1.0f}));
    rclcpp::Parameter param("SwingPeriod_LIMITS", std::vector<float>({}));
    this->get_parameter("SwingPeriod_LIMITS", param);
    std::vector<double> test = param.as_double_array();
    SwingPeriod_LIMITS[0] = (float) test[0];
    SwingPeriod_LIMITS[1] = (float) test[1];

    

    /* Stock, use arrow pads to change */
    this->declare_parameter("BaseClearanceHeight",0.0f);
    BaseClearanceHeight = (float) this->get_parameter("BaseClearanceHeight").as_double();
    ClearanceHeight = BaseClearanceHeight;

    this->declare_parameter("BasePenetrationDepth",0.0f);
    BasePenetrationDepth = (float) this->get_parameter("BasePenetrationDepth").as_double();
    PenetrationDepth = BasePenetrationDepth;

    this->declare_parameter("ClearanceHeight_LIMITS", std::vector<float>({0.0f, 1.0f}));
    auto param2 = this->get_parameter("ClearanceHeight_LIMITS");
    ClearanceHeight_LIMITS[0] = (float)param2.as_double_array()[0];
    ClearanceHeight_LIMITS[1] = (float)param2.as_double_array()[1];

    this->declare_parameter("PenetrationDepth_LIMITS", std::vector<float>({0.0f, 1.0f}));
    auto param3 = this->get_parameter("PenetrationDepth_LIMITS");
    PenetrationDepth_LIMITS[0] = (float)param3.as_double_array()[0];
    PenetrationDepth_LIMITS[1] = (float)param3.as_double_array()[1];

    /* ############## CONTROL VARIABLEs ############## */
    /* joint angles in dictionary */
    joint_angles << 0, 0, 0, 0, 0, 0, 0, 0, 0, 0, 0, 0;
    
    /* joint currents in dictionary */
    joint_currents << 0, 0, 0, 0, 0, 0, 0, 0, 0, 0, 0, 0;

    /* Flag to signal when angles and currents have already been measured atleast once */
    readflag_data = false;
    config_done = false;
    current_set = false;

    mini_cmd.x_velocity = 0.0f;
    mini_cmd.y_velocity = 0.0f;
    mini_cmd.rate = 0.0f;
    mini_cmd.roll = 0.0f;
    mini_cmd.pitch = 0.0f;
    mini_cmd.yaw = 0.0f;
    mini_cmd.z = 0.0f;
    mini_cmd.motion = "Stop";
    mini_cmd.movement = "Stepping";

    /* IMU: R, P, Ax, Ay, Az, Gx, Gy, Gz */
    for (int i = 0; i < 8; i++) {
        imu[i] = 0.0f;
    }

    /* Time */
    time_now = this->get_clock()->now();

    /* Kinematic model of quaduped */
    this->declare_parameter("shoulder_length",0.0f);
    this->declare_parameter("elbow_length",0.0f);
    this->declare_parameter("wrist_length",0.0f);
    this->declare_parameter("hip_x",0.0f);
    this->declare_parameter("hip_y",0.0f);
    this->declare_parameter("foot_x",0.0f);
    this->declare_parameter("foot_y",0.0f);
    this->declare_parameter("height",0.0f);
    this->declare_parameter("com_offset",0.0f);

    com_offset = (float) this->get_parameter("com_offset").as_double();

    quadKine = QuadModel((float) this->get_parameter("shoulder_length").as_double(),
                         (float) this->get_parameter("elbow_length").as_double(),
                         (float) this->get_parameter("wrist_length").as_double(),
                         (float) this->get_parameter("hip_x").as_double(),
                         (float) this->get_parameter("hip_y").as_double(),
                         (float) this->get_parameter("foot_x").as_double(),
                         (float) this->get_parameter("foot_y").as_double(),
                         (float) this->get_parameter("height").as_double(),
                         com_offset);                

    T_bf0 = quadKine.WorldToFoot;
    T_bf = T_bf0;
    T_bh = quadKine.WorldToHip;

    std::map<uint8_t, Eigen::Vector3f>  T_hf;
    T_hf.insert(std::pair<uint8_t, Eigen::Vector3f>(FL, {0.0f ,0.0f, 0.0f}));
    T_hf.insert(std::pair<uint8_t, Eigen::Vector3f>(FR, {0.0f ,0.0f, 0.0f}));
    T_hf.insert(std::pair<uint8_t, Eigen::Vector3f>(BL, {0.0f ,0.0f, 0.0f}));
    T_hf.insert(std::pair<uint8_t, Eigen::Vector3f>(BR, {0.0f ,0.0f, 0.0f}));

    quadKine.HipToFoot(Eigen::Vector3f {0,0,0}, Eigen::Vector3f {com_offset,0,0}, T_bf, &T_hf);

    desired[0] = T_hf[FL];
    desired[1] = T_hf[FR];
    desired[2] = T_hf[BL];
    desired[3] = T_hf[BR];

    this->declare_parameter("dt", 1.0);
    // Phase Lag Per Leg: FL, FR, BL, BR
    std::array<float, 4> dSref = {0.0f, 0.5f, 0.5f, 0.0f};
    std::array<float, 4> dSref_end = {0.0f, 0.0f, 0.0f, 0.0f};
    // std::array<float, 4> dSref = {0.0f, 0.5f, 0.5f, 0.0f};
    bzg = BezierGait(dSref, dSref_end, (float) this->get_parameter("dt").as_double(), BaseSwingPeriod, STEPLENGTH_SCALE);

    
    /* ############## SUBSCRIBERS ############## */

    client_cb_group_ = this->create_callback_group(rclcpp::CallbackGroupType::Reentrant);
    timer_cb_group_ = client_cb_group_;
    rclcpp::SubscriptionOptions options;
    options.callback_group = client_cb_group_;

    sub_cmd = this->create_subscription<joint_msgs::msg::MiniCmd>("mini_cmd",1,
    std::bind(&RealInterface::cmd_cb, this, _1));

    sub_jb = this->create_subscription<teleop_msgs::msg::JoyButtons>("joybuttons",1,
    std::bind(&RealInterface::jb_cb, this, _1));


    jbreleased = true;
    sbreleased = true;
    start_movement = false;
    standing = true;
    motor_states = 0;
    uptime = 3;
    stood = false;
    descend = false;

    /* Subscription in charge of receiving new data */
    subscription_joint_data = this->create_subscription<joint_msgs::msg::OdriveData>("joint_data",
    10,std::bind(&RealInterface::update_data, this, _1), options);

    errors_data = this->create_subscription<error_msgs::msg::Error>("error_state",
    10,std::bind(&RealInterface::error_update, this, _1), options);

    sub_imu = this->create_subscription<custom_sensor_msgs::msg::IMUdata>("IMU",
    10,std::bind(&RealInterface::imu_cb, this, _1));

    /* ############## PUBLISHERS ############## */
    ja_pub = this->create_publisher<joint_msgs::msg::Joints>("joint_requests",1);
    motor_state = this->create_publisher<std_msgs::msg::Bool>("motors_state",1);

    publish_max_currents = this->create_publisher<joint_msgs::msg::Joints>("joint_max_currents",2);

    traj = Trajectories(POLYNOMIAL);

    timer_ = create_wall_timer(
        std::chrono::milliseconds(1000/80),
        std::bind(&RealInterface::control, this), timer_cb_group_
    );

    RCLCPP_INFO(rclcpp::get_logger("rclcpp"),"READY TO GO!");
}

void RealInterface::imu_cb(const custom_sensor_msgs::msg::IMUdata::SharedPtr data)
{
    imu[0] = data->roll;
    imu[1] = data->pitch;
    imu[2] = (data->gyro_x) * (M_PI / 180);
    imu[3] = (data->gyro_y) * (M_PI / 180);
    imu[4] = (data->gyro_z) * (M_PI / 180);
    imu[5] = data->acc_x;
    imu[6] = data->acc_y;
    imu[7] = (data->acc_z) - 9.81;
}

void RealInterface::error_update(error_msgs::msg::Error::SharedPtr data)
{
    if (data->motor_error != 0)
    {
        RCLCPP_INFO(rclcpp::get_logger("rclcpp"),"Motor Error Detected, Shuting down");
        ERROR_STATE = 1;
        std_msgs::msg::Bool msg;
        msg.data = false;
        motor_states = 0;
        motor_state->publish(msg);
    }

}

void RealInterface::update_data(joint_msgs::msg::OdriveData::SharedPtr data)
{
    joint_angles << data->angles.flshoulder, data->angles.flarm, data->angles.flfoot,
                    data->angles.frshoulder, data->angles.frarm, data->angles.frfoot,
                    data->angles.blshoulder, data->angles.blarm, data->angles.blfoot,
                    data->angles.brshoulder, data->angles.brarm, data->angles.brfoot;  

    joint_currents << data->currents.flshoulder, data->currents.flarm, data->currents.flfoot,
                      data->currents.frshoulder, data->currents.frarm, data->currents.frfoot,
                      data->currents.blshoulder, data->currents.blarm, data->currents.blfoot,
                      data->currents.brshoulder, data->currents.brarm, data->currents.brfoot;

    if (!readflag_data){
        readflag_data = true;
    }
}

void RealInterface::cmd_cb(joint_msgs::msg::MiniCmd::SharedPtr data)
{
    mini_cmd.motion = data->motion;
    mini_cmd.movement = data->movement;
    mini_cmd.x_velocity = data->x_velocity;
    mini_cmd.y_velocity = data->y_velocity;
    mini_cmd.rate = data->rate;
    mini_cmd.roll = data->roll;
    mini_cmd.pitch = data->pitch;
    mini_cmd.yaw = data->yaw;
    mini_cmd.z = data->z;
    mini_cmd.faster = data->faster;
    mini_cmd.slower = data->slower;
}

void RealInterface::jb_cb(teleop_msgs::msg::JoyButtons::SharedPtr data)
{
    jb.updown = data->updown;
    jb.leftright = data->leftright;
    jb.left_bump = data->left_bump;
    jb.right_bump = data->right_bump;
    jb.start_b = data->start_b;

    if (ERROR_STATE == 0)
    {
        if (data->left_bump && jbreleased){
            std_msgs::msg::Bool msg;
            if (motor_states == 0){
                msg.data = true;
                motor_states = 1;
            } else {
                msg.data = false;
                motor_states = 0;
            }
            motor_state->publish(msg);
            jbreleased = false;
        }
        if (!data->left_bump){
            jbreleased = true;
        }
        
        if (data->start_b && sbreleased && !start_movement)
        {
            RCLCPP_INFO(rclcpp::get_logger("rclcpp"),"Movement started!");
            start_movement = true;
            sbreleased = false;
            MatrixJoint xyz = get_xyz();
            stood = true;

            uint8_t index = 0;
            for (auto& pair : T_bh) {
                Eigen::Matrix4f foot = pair.second;
                
                foot.block(0,3,3,1) += xyz.block(index,0,1,3).transpose();
                pair.second = foot;
                adder.block(index,0,1,3) = desired[index].transpose() - xyz.block(index,0,1,3);
                index++;
            }

            upt0 = this->get_clock()->now();
        } else if (data->start_b && sbreleased && !standing && stood)
        {
            descend = true;
            upt0 = this->get_clock()->now();
        }

        if (!data->start_b) {
            sbreleased = true;
        }
    }
    
}

void RealInterface::set_current(uint8_t max_current){
    RCLCPP_INFO(rclcpp::get_logger("rclcpp"),(std::string("Configuring currents to ") + std::to_string(max_current)).c_str());
    joint_msgs::msg::Joints msg;   
    msg.flshoulder = max_current;
    msg.flarm = max_current;
    msg.flfoot = max_current;
    msg.frshoulder = max_current;
    msg.frarm = max_current;
    msg.frfoot = max_current;
    msg.blshoulder = max_current;
    msg.blarm = max_current;
    msg.blfoot = max_current;
    msg.brshoulder = max_current;
    msg.brarm = max_current;
    msg.brfoot = max_current;
    publish_max_currents->publish(msg);
}
    
void RealInterface::control(){
    if (ERROR_STATE == 0)
    {
        if (!config_done) {
            if (!current_set) {
                set_current(MAX_CURRENT);
                current_set = true;
            }
            if (readflag_data && current_set) {
                config_done = true;
            }
        } else if (start_movement) {
            rclcpp::Time tnow;
            if (standing){
                tnow = this->get_clock()->now();
                rclcpp::Duration duration = tnow - upt0;
                if (duration.seconds() > uptime) {
                    standing = false;
                    RCLCPP_INFO(rclcpp::get_logger("rclcpp"),"Done Standing");
                } else {
                    rclcpp::Duration tmove = tnow - upt0;
                    TransfDict T_bh_command = T_bh;
                    uint8_t index = 0;
                    for (auto& pair : T_bh_command) {
                        Eigen::Matrix4f foot = pair.second;
                        foot.block(0,3,3,1) += adder.block(index++,0,1,3).transpose()*traj.get_value(tmove.seconds()/uptime);
                        pair.second = foot;
                    }

                    MatrixJoint ja = quadKine.IK({0,0,0}, {-com_offset,0,0}, T_bh_command);

                    publishall(ja);
                }
            } else if (descend) {
                tnow = this->get_clock()->now();
                rclcpp::Duration duration = tnow - upt0;
                if (duration.seconds() > uptime) {
                    std_msgs::msg::Bool msg;
                    msg.data = false;
                    motor_states = 0;
                    motor_state->publish(msg);
                    start_movement = false;
                } else {
                    TransfDict T_bh_command = T_bh;
                    uint8_t index = 0;
                    for (auto& pair : T_bh_command) {
                        Eigen::Matrix4f foot = pair.second;
                        
                        foot.block(0,3,3,1) += adder.block(index++,0,1,3).transpose()*(1-traj.get_value(duration.seconds()/uptime));
                        pair.second = foot;
                    }
                    MatrixJoint ja = quadKine.IK({0,0,0}, {-com_offset,0,0}, T_bh_command);
                    publishall(ja);
                }
            } else {
                move();
            }
        }
    }
    
    
}

MatrixJoint RealInterface::get_xyz()
{
    MatrixJoint xyz = quadKine.FK(joint_angles);
    return xyz;
}
    
void RealInterface::move(){
    Eigen::Vector3f pos = {0.0f, 0.0f ,0.0f};
    Eigen::Vector3f orn = {0.0f ,0.0f ,0.0f};
    float StepLength = 0.0f;
    float LateralFraction = 0.0f;
    float YawRate = 0.0f;


    if (mini_cmd.motion != "Stop")
    {
        StepVelocity = BaseStepVelocity;
        SwingPeriod = std::max(
                        std::min(BaseSwingPeriod + (-mini_cmd.faster - mini_cmd.slower) * SV_SCALE,
                                 SwingPeriod_LIMITS[1]),
                        SwingPeriod_LIMITS[0]);
        

        if (mini_cmd.movement == "Stepping") {
            StepLength = mini_cmd.x_velocity + std::fabs(mini_cmd.y_velocity * 0.66f);
            StepLength = std::max( std::min(StepLength,1.0f), -1.0f);
            StepLength *= STEPLENGTH_SCALE;
            LateralFraction = mini_cmd.y_velocity * M_PI / 2;
            YawRate = mini_cmd.rate * YAW_SCALE;
            pos << 0.0f, 0.0f, 0.0f;
            orn << 0.0f, 0.0f, 0.0f;

        } else {
            StepLength = 0.0f;
            LateralFraction = 0.0f;
            YawRate = 0.0f;

            ClearanceHeight = BaseClearanceHeight;
            PenetrationDepth = BasePenetrationDepth;
            StepVelocity = BaseStepVelocity;

            pos << 0.0f, 0.0f, mini_cmd.z * Z_SCALE_CTRL;
            orn << mini_cmd.roll * RPY_SCALE, mini_cmd.pitch * RPY_SCALE, mini_cmd.yaw * RPY_SCALE;
        }
    } else {
        StepLength = 0.0f;
        LateralFraction = 0.0f;
        YawRate = 0.0f;

        ClearanceHeight = BaseClearanceHeight;
        PenetrationDepth = BasePenetrationDepth;
        StepVelocity = BaseStepVelocity;
        SwingPeriod = BaseSwingPeriod;
        pos << 0.0f, 0.0f, 0.0f;
        orn << 0.0f, 0.0f, 0.0f;
    }
    
    ClearanceHeight += jb.updown * CHPD_SCALE;
    PenetrationDepth += jb.leftright * CHPD_SCALE;

    if (jb.right_bump){
        ClearanceHeight = BaseClearanceHeight;
        PenetrationDepth = BasePenetrationDepth;
        StepVelocity = BaseStepVelocity;
        SwingPeriod = BaseSwingPeriod;
    }
    
    rclcpp::Time tnow;
    tnow = this->get_clock()->now();
    rclcpp::Duration dt = tnow - time_now;

    time_now = tnow;

    bzg.Tswing_ref = SwingPeriod;

    ClearanceHeight = std::max(
                            std::min(ClearanceHeight, ClearanceHeight_LIMITS[1]),
                            ClearanceHeight_LIMITS[0]);

    PenetrationDepth = std::max(
                            std::min(PenetrationDepth, PenetrationDepth_LIMITS[1]),
                            PenetrationDepth_LIMITS[0]);

    
    T_bf = bzg.GenerateTrajectory(StepLength, LateralFraction,
                                            YawRate, StepVelocity,
                                            T_bf0,
                                            ClearanceHeight,
                                            PenetrationDepth,
                                            dt.seconds());

    TransfDict T_bf_copy = T_bf;

    MatrixJoint angles_now = quadKine.IK(orn, pos, T_bf_copy);

    publishall(angles_now);
}

void RealInterface::publishall(MatrixJoint angles){
    joint_msgs::msg::Joints ja_msg;
    
    /*
    ja_msg.header.stamp.sec = int(np.floor(t))
    ja_msg.header.stamp.nanosec = int((t - np.floor(t))*1000000000)
    */

    ja_msg.flshoulder = angles(0, 0) * 180/M_PI;
    ja_msg.flarm = angles(0, 1) * 180/M_PI;
    ja_msg.flfoot = angles(0, 2) * 180/M_PI;

    ja_msg.frshoulder = angles(1, 0) * 180/M_PI;
    ja_msg.frarm = angles(1, 1) * 180/M_PI;
    ja_msg.frfoot = angles(1, 2) * 180/M_PI;

    ja_msg.blshoulder = angles(2, 0) * 180/M_PI;
    ja_msg.blarm = angles(2, 1) * 180/M_PI;
    ja_msg.blfoot = angles(2, 2) * 180/M_PI;

    ja_msg.brshoulder = angles(3, 0) * 180/M_PI;
    ja_msg.brarm = angles(3, 1) * 180/M_PI;
    ja_msg.brfoot = angles(3, 2) * 180/M_PI;

    ja_msg.motion = mini_cmd.motion;
    ja_msg.movement = mini_cmd.movement;

    ja_msg.header.stamp = rclcpp::Clock(RCL_ROS_TIME).now();
    ja_pub->publish(ja_msg);
}

int main(int argc, char * argv[])
{
  rclcpp::init(argc, argv);
  rclcpp::spin(std::make_shared<RealInterface>());
  rclcpp::shutdown();
  return 0;
}

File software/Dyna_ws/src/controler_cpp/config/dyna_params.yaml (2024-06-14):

/interface:
  ros__parameters:
    # MEASURE
    # COM to Shoulder
    shoulder_length: 0.0435
    # Shoulder to Elbow
    elbow_length: 0.190
    # Elbow to Wrist
    wrist_length: 0.194
    # Forward Hip Separation
    hip_x: 0.470447   #0.455
    # Lateral Hip Separation
    hip_y: 0.197

    # ADJUSTABLE
    # Stance Length
    foot_x: 0.470447 # 0.455
    # Stance Width
    foot_y: 0.297
    # Stance Height
    height: 0.32 # 0.20
    # Adjust for balanced walk
    com_offset: -0.05
  

    # Time Step
    dt: 0.0125

    # Swing Period (lower is faster)
    Tswing: 0.18  # 0.2
    SwingPeriod_LIMITS: [0.1, 0.35]

    # Step Velocity (Using very low value as my main form of speed control is swing period)
    BaseStepVelocity: 0.5

    # Foot Clearance Height
    BaseClearanceHeight: 0.05  # 0.035
    ClearanceHeight_LIMITS: [0.0, 0.05]  # [0.0, 0.04]

    # Foot Penetration Depth
    BasePenetrationDepth: 0.003
    PenetrationDepth_LIMITS: [0.0, 0.02]

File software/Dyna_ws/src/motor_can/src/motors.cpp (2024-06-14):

#include "motors.hpp"

using std::placeholders::_1;

Motors::Motors(): Node("brushless_motors")
{
    RCLCPP_INFO(rclcpp::get_logger("rclcpp"),"Staring Motor Node");
    this->declare_parameter("fileLocation", "");
    rclcpp::QoS rmw_qos_profile_sensor_data(24);

    client_cb_group_ = this->create_callback_group(rclcpp::CallbackGroupType::Reentrant);
    timer_cb_group_ = client_cb_group_;
    rclcpp::SubscriptionOptions options;
    options.callback_group = client_cb_group_;

    publisher_CAN = this->create_publisher<can_msgs::msg::Frame>("CAN/can0/transmit",24);
    subscriber_CAN = this->create_subscription<can_msgs::msg::Frame>("CAN/can0/receive",
                                                        24,
                                                        std::bind(&Motors::reception, this, _1),
                                                        options);

    subscriber_state= this->create_subscription<std_msgs::msg::Bool>("/motors_state",10,
    std::bind(&Motors::change_state, this, _1));

    subscriber_joints = this->create_subscription<joint_msgs::msg::Joints>("joint_requests",1000,
    std::bind(&Motors::request, this, _1), options);
    
    subscriber_max_current = this->create_subscription<joint_msgs::msg::Joints>("joint_max_currents",1000,
    std::bind(&Motors::change_max_current, this, _1));

    publisher_odrive_data = this->create_publisher<joint_msgs::msg::OdriveData>("joint_data",100);
    
    timer_ = create_wall_timer(
        std::chrono::milliseconds(10),
        std::bind(&Motors::publish_joints, this), timer_cb_group_
    );
    
    const std::string jsonFilePath = this->get_parameter("fileLocation").as_string();
    std::ifstream jsonFile(jsonFilePath);  
    if (jsonFile.is_open()) {
        jsonFile >> leg_data;
        jsonFile.close();
    } else {
        std::cout << "Failed to open JSON file" << std::endl;
    }

    canEncDec = CanED();

    // Front Right

    brushless_motors.insert(std::pair<std::string, BrushlessMotor>("FRshoulder", BrushlessMotor(
            static_cast<uint8_t>(leg_data["FR"]["motor0"]["motorN"].asUInt()),
            leg_data["FR"]["motor0"]["iOffset"].asFloat(),
            static_cast<uint8_t>(leg_data["FR"]["motor0"]["axisID"].asUInt()),
            static_cast<int8_t>(leg_data["FR"]["motor0"]["direction"].asInt()),
            "FRshoulder")));
    
    brushless_motors.insert(std::pair<std::string, BrushlessMotor>("FRarm", BrushlessMotor(
            static_cast<uint8_t>(leg_data["FR"]["motor1"]["motorN"].asUInt()),
            leg_data["FR"]["motor1"]["iOffset"].asFloat(),
            static_cast<uint8_t>(leg_data["FR"]["motor1"]["axisID"].asUInt()),
            static_cast<int8_t>(leg_data["FR"]["motor1"]["direction"].asInt()),
            "FRarm")));
    
    brushless_motors.insert(std::pair<std::string, BrushlessMotor>("FRfoot", BrushlessMotor(
            static_cast<uint8_t>(leg_data["FR"]["motor2"]["motorN"].asUInt()),
            leg_data["FR"]["motor2"]["iOffset"].asFloat(),
            static_cast<uint8_t>(leg_data["FR"]["motor2"]["axisID"].asUInt()),
            static_cast<int8_t>(leg_data["FR"]["motor2"]["direction"].asInt()),
            "FRfoot")));

    // Front Left

    brushless_motors.insert(std::pair<std::string, BrushlessMotor>("FLshoulder", BrushlessMotor(
            static_cast<uint8_t>(leg_data["FL"]["motor0"]["motorN"].asUInt()),
            leg_data["FL"]["motor0"]["iOffset"].asFloat(),
            static_cast<uint8_t>(leg_data["FL"]["motor0"]["axisID"].asUInt()),
            static_cast<int8_t>(leg_data["FL"]["motor0"]["direction"].asInt()),
            "FLshoulder")));
    
    brushless_motors.insert(std::pair<std::string, BrushlessMotor>("FLarm", BrushlessMotor(
            static_cast<uint8_t>(leg_data["FL"]["motor1"]["motorN"].asUInt()),
            leg_data["FL"]["motor1"]["iOffset"].asFloat(),
            static_cast<uint8_t>(leg_data["FL"]["motor1"]["axisID"].asUInt()),
            static_cast<int8_t>(leg_data["FL"]["motor1"]["direction"].asInt()),
            "FLarm")));

    brushless_motors.insert(std::pair<std::string, BrushlessMotor>("FLfoot", BrushlessMotor(
            static_cast<uint8_t>(leg_data["FL"]["motor2"]["motorN"].asUInt()),
            leg_data["FL"]["motor2"]["iOffset"].asFloat(),
            static_cast<uint8_t>(leg_data["FL"]["motor2"]["axisID"].asUInt()),
            static_cast<int8_t>(leg_data["FL"]["motor2"]["direction"].asInt()),
            "FLfoot")));

    // Back Left

    brushless_motors.insert(std::pair<std::string, BrushlessMotor>("BLshoulder", BrushlessMotor(
            static_cast<uint8_t>(leg_data["BL"]["motor0"]["motorN"].asUInt()),
            leg_data["BL"]["motor0"]["iOffset"].asFloat(),
            static_cast<uint8_t>(leg_data["BL"]["motor0"]["axisID"].asUInt()),
            static_cast<int8_t>(leg_data["BL"]["motor0"]["direction"].asInt()),
            "BLshoulder")));
    
    brushless_motors.insert(std::pair<std::string, BrushlessMotor>("BLarm", BrushlessMotor(
            static_cast<uint8_t>(leg_data["BL"]["motor1"]["motorN"].asUInt()),
            leg_data["BL"]["motor1"]["iOffset"].asFloat(),
            static_cast<uint8_t>(leg_data["BL"]["motor1"]["axisID"].asUInt()),
            static_cast<int8_t>(leg_data["BL"]["motor1"]["direction"].asInt()),
            "BLarm")));

    brushless_motors.insert(std::pair<std::string, BrushlessMotor>("BLfoot", BrushlessMotor(
            static_cast<uint8_t>(leg_data["BL"]["motor2"]["motorN"].asUInt()),
            leg_data["BL"]["motor2"]["iOffset"].asFloat(),
            static_cast<uint8_t>(leg_data["BL"]["motor2"]["axisID"].asUInt()),
            static_cast<int8_t>(leg_data["BL"]["motor2"]["direction"].asInt()),
            "BLfoot")));

    // Back Right

    brushless_motors.insert(std::pair<std::string, BrushlessMotor>("BRshoulder", BrushlessMotor(
            static_cast<uint8_t>(leg_data["BR"]["motor0"]["motorN"].asUInt()),
            leg_data["BR"]["motor0"]["iOffset"].asFloat(),
            static_cast<uint8_t>(leg_data["BR"]["motor0"]["axisID"].asUInt()),
            static_cast<int8_t>(leg_data["BR"]["motor0"]["direction"].asInt()),
            "BRshoulder")));
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

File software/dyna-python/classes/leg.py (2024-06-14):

from classes.leg_math import for_k, f2t, w2v
from classes.brushless_CAN import BrushlessMotor
import time
import math
from classes.leg_kinematics import LegK

class Leg:
    """
    The Leg class handles everything related to the Dyna-1 leg. All cartesian
    positions are measured in meters. From a top perspective the X axis is 
    forward, the Y axis is to the left and the Z axis is out of the page
    """

    def __init__(self, name, leg_data, odrv_center = None):
        """
        When initializing the user can select wether or not to search for an index.
        Thanks to the Odrive internal memory, if the index is already found, as long
        as its not rebooted it doesn't have to be searched for again
        :param index_search: (optional) boolean to set if index search is desired
        """
        self.name = name

        self.L1 = 0.0435 # Servo link length
        self.L2 = 0.190 # Link 1 length
        self.L3 = 0.194 # link 2 length

        self.rrate = 9 # reduction rate
        
        self.motor0 = BrushlessMotor(leg_data["motor0"]["motorN"],
                                     leg_data["motor0"]["iOffset"],
                                     leg_data["motor0"]["axisID"],
                                     leg_data["motor0"]["direction"],
                                     odrive_instance = odrv_center)
            
        self.motor1 = BrushlessMotor(leg_data["motor1"]["motorN"],
                                     leg_data["motor1"]["iOffset"],
                                     leg_data["motor1"]["axisID"],
                                     leg_data["motor1"]["direction"])

        self.motor2 = BrushlessMotor(leg_data["motor2"]["motorN"],
                                     leg_data["motor2"]["iOffset"],
                                     leg_data["motor2"]["axisID"],
                                     leg_data["motor2"]["direction"],
                                     odrive_instance = self.motor1.odrive)

        self.legKinematics = LegK(legtype = leg_data["legType"],
                                  shoulder_length = self.L1,
                                  elbow_length = self.L2,
                                  wrist_length = self.L3)
        
        self.motors = [self.motor0, self.motor1, self.motor2]


    def find_index(self, axis = [0, 1, 2]):
        for axi in axis:
            input(f'Ready to search for index of axis {axi} of {self.name}?')
            self.motors[axi].index_search()


    def IK(self, pos):
        """
        IK takes the cartesian position of the end effector and returns the
        corresponding angles
        :param pos: cartesian position in meters with respect to the leg axis
                    in a list of the form [x, y, z]
        :return: corresponding angles in degrees in a list [t0, t1, t2]
        """
        return self.legKinematics.solveIK(pos)
    

    def FK(self, ang):
        """
        FK takes the leg angles and returns the corresponding cartesian position
        :param ang: leg angles in degrees in a list [t0, t1, t2]
        :return: cartesian position in meters with respect to the leg axis in
                 a list [x, y, z]
        """
        return self.legKinematics.solveFK(ang)

    def get_motor_positions(self, n=1):
        """
        get_angle returns all the motor angles in degrees. An optional input can
        set how many measurements to average over.
        :param n: (optional) number of measurements to average over
        :return: measured leg angles in degrees in the form of a list [t0, t1, t2]
        """
        t0 = 0
        t1 = 0
        t2 = 0
        for i in range(1,n+1): # calculating the average
            t0 += (self.motor0.get_position() - t0)/i # brushless angle is divided by reduction rate
            t1 += (self.motor1.get_position() - t1)/i # brushless angle is divided by reduction rate
            t2 += (self.motor2.get_position() - t2)/i # brushless angle is divided by reduction rate
        return [t0, t1, t2]

    def set_zero_positions(self, positions):
        for motor, pos in zip(self.motors, positions):
            motor.set_pos0(pos)

    def get_angle(self, n=1):
        """
        get_angle returns all the motor angles in degrees. An optional input can
        set how many measurements to average over.
        :param n: (optional) number of measurements to average over
        :return: measured leg angles in degrees in the form of a list [t0, t1, t2]
        """
        t0 = 0
        t1 = 0
        t2 = 0
        for i in range(1,n+1): # calculating the average
            t0 += (self.motor0.get_angle()/self.rrate - t0)/i # brushless angle is divided by reduction rate
            t1 += (self.motor1.get_angle()/self.rrate - t1)/i # brushless angle is divided by reduction rate
            t2 += (self.motor2.get_angle()/self.rrate - t2)/i # brushless angle is divided by reduction rate
        return [t0, t1, t2]
    

    def get_position(self, n=1):
        """
        get_position returns the current cartesian position of the end effector. Can
        optionally average over various measurements
        :param n: (optional) number of measurements to average over
        :return: list of cartesian positions in meters ([x, y, z])
        """
        return self.FK(self.get_angle(n))
    

    def turn_on(self,):
        """
        turn_on turns on all motors
        """
        self.motor0.turn_on()
        self.motor1.turn_on()
        self.motor2.turn_on()
    

    def turn_off(self):
        """
        turn_off turns off all motors
        """
        self.motor0.turn_off()
        self.motor1.turn_off()
        self.motor2.turn_off()
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

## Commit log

2024-06-10 software dump
    [BOM.xlsx, Body.stl, arm1.stl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]
2024-06-11 more dump
    [control.csv, currents.csv, imu.csv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]
2025-04-21 first enviroment isaaclab working version
    [dyna1.urdf, dyna1_gazebo.urdf, dyna1_gazebo3.urdf]
2026-02-21 Replace ext_template with DynabotIsaacTemplate
    [dyna1.urdf, dyna1_gazebo.urdf, dyna1_gazebo3.urdf]
